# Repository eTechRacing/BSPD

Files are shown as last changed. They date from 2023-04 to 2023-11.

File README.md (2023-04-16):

# BSPD

This repository contains the hardware design files for the Brake System Plausibility Device (BSPD) used in e-Tech Racing's electric vehicle.

## Purpose
The BSPD is a non-programmable circuit that ensures the safe operation of the vehicle during hard braking events. The BSPD must open the shutdown circuit when hard braking occurs, if more than 5kW of power is being delivered to the motors for more than 500ms.

### ⚠️Warning⚠️
Please check for changes in ruling. This BSPD is designed following [FSG Rules from 2023](https://www.formulastudent.de/fileadmin/user_upload/all/2023/rules/FS-Rules_2023_v1.1.pdf).
This version of the BSPD is normally closed when not powered. This could be a potential rules issue, so consider redesigning the relay part for this to be solved.

## Additional hardware
For the BSPD to work, two sensors and a 20-30VDC supply are needed. Here are the ones used in ETR-08:
- [Brake pressure sensor](https://www.amazon.es/gp/product/B07HLKD5L1/ref=ppx_yo_dt_b_asin_title_o01_s00?ie=UTF8&psc=1) : 0.5-4.5V, 1/8", supplied with 5VDC. Bought via Amazon, 25€
- [Hall current sensor](https://www.lem.com/en/product-list/has-100s): In order to measure power, a current sensor is used, so worst case scenario is 5kW / Vmax = 8.5A.

## Installation
- To use the BSPD, follow the installation steps below:

- Connect the brake system pressure sensor to the BSPD.

- Connect the TS current sensor to the BSPD.

- Connect the BSPD to the LVMS.

- Test the BSPD to ensure proper functionality.

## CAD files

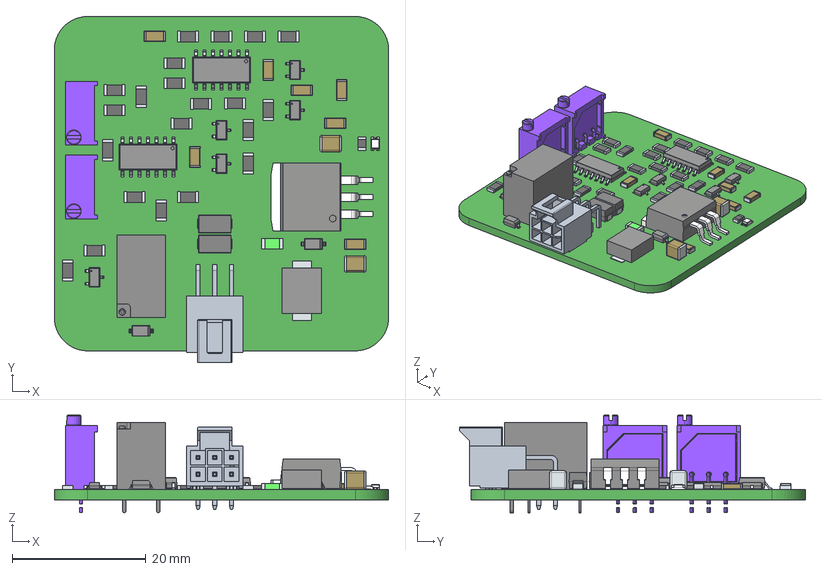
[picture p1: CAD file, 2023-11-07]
BSPD/BSPD_PCB/Project Outputs for BSPD/ExportSTEP/BSPD.step
50.0 x 51.7 x 14.6 mm
3296W-1-100LF x 8
term1 x 23
term2 x 23
150080RS75000
G5V-1-DC5_RGB4408131
PinsArrayLR x 2
BODY-TO
HTSINK-TO263
LEAD-TO263 x 3
PinsArrayL x 5
FilletPinR x 7
FilletPinL x 2
FilletPin1 x 2
FilletPin2 x 2
Pins

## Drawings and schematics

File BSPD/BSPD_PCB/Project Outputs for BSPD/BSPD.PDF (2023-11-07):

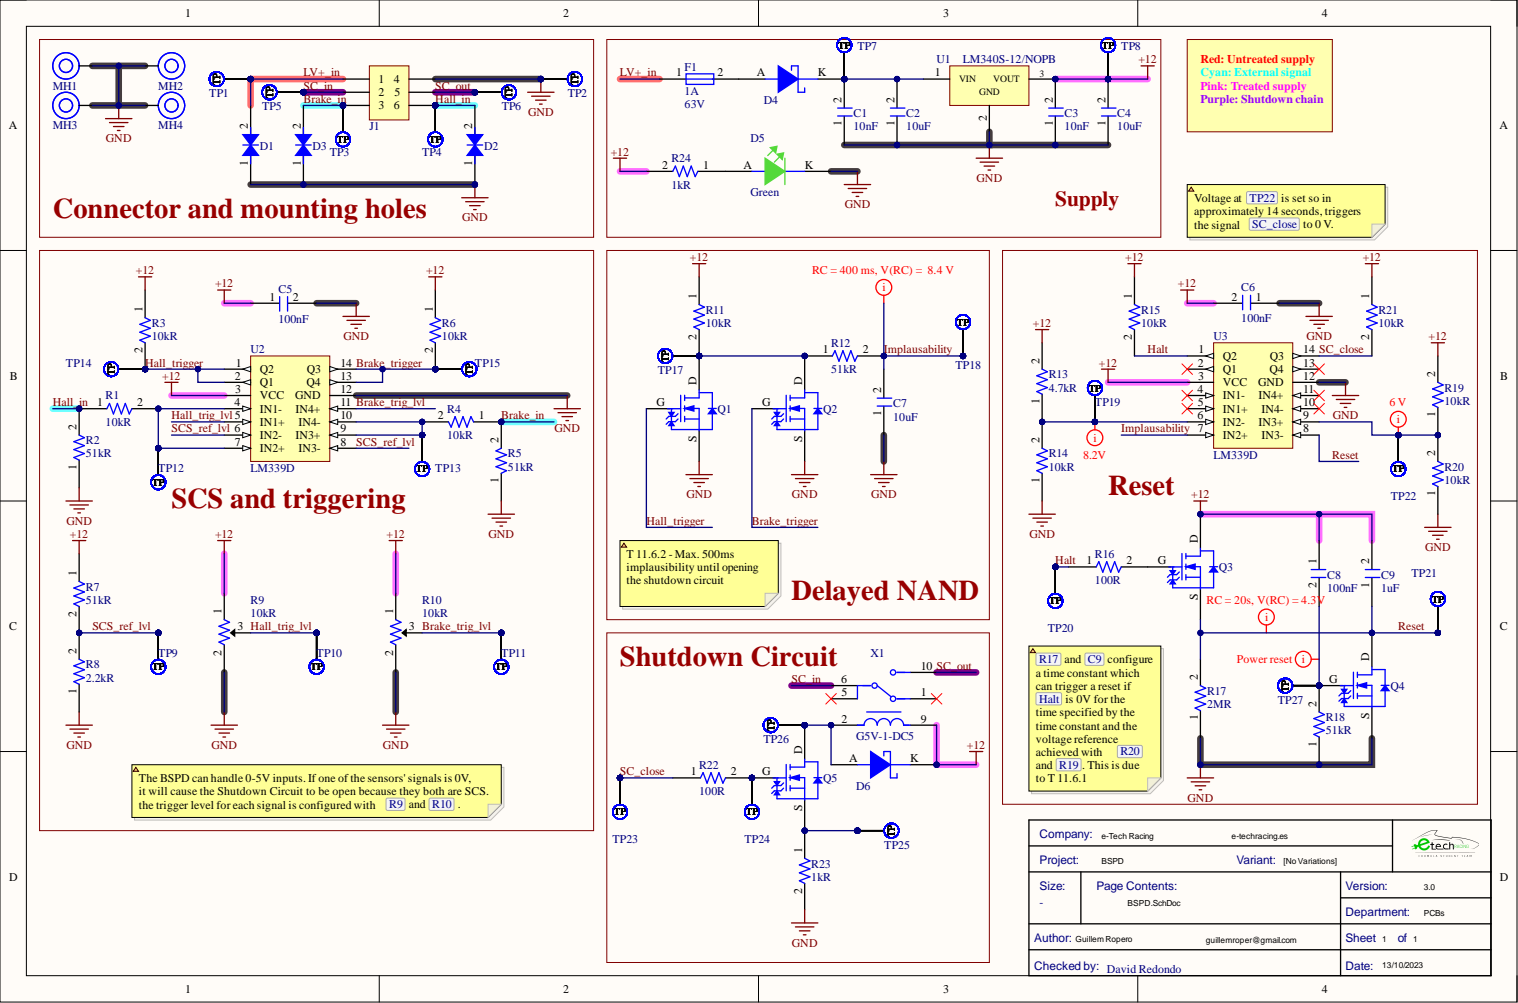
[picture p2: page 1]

Voltage at TP22 is set so in
approximately 14 seconds, triggers
the signal SC_close to 0 V.

Connector and mounting holes

R17 and C9 configure
a time constant which
can trigger a reset if
Halt is 0V for the
time specified by the
time constant and the
voltage reference
and R19 . This is due

The BSPD can handle 0-5V inputs. If one of the sensors' signals is 0V,
it will cause the Shutdown Circuit to be open because they both are SCS.

Author: Guillem Ropero guillemroper@gmail.com | Sheet 1 of 1

Checked by: David Redondo | Date: 13/10/2023

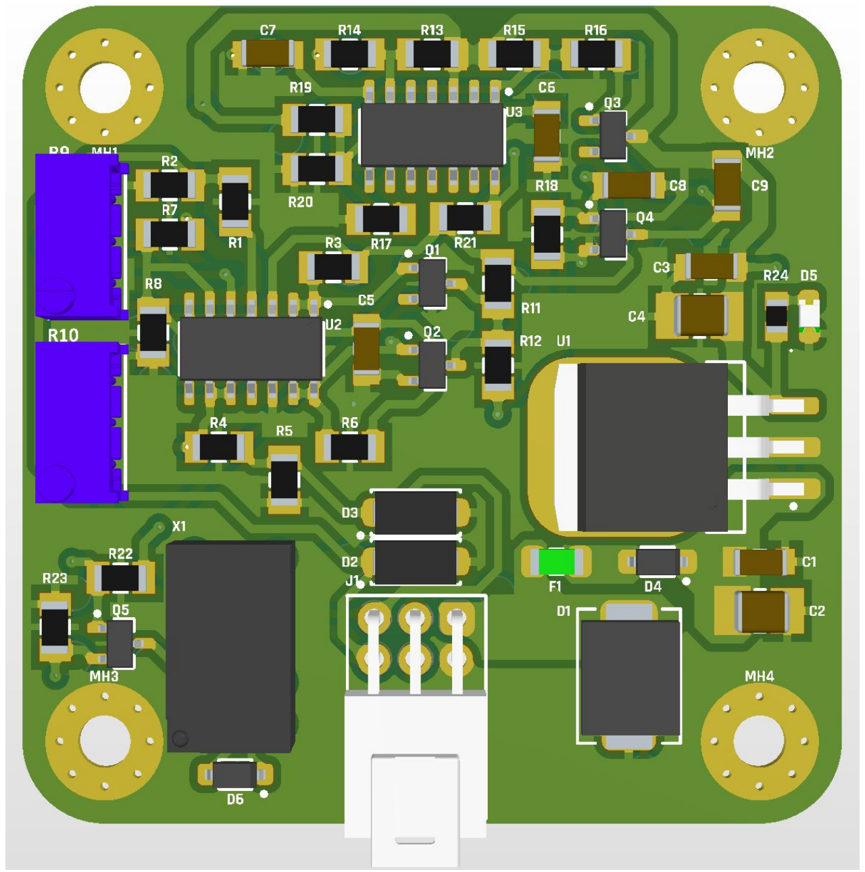
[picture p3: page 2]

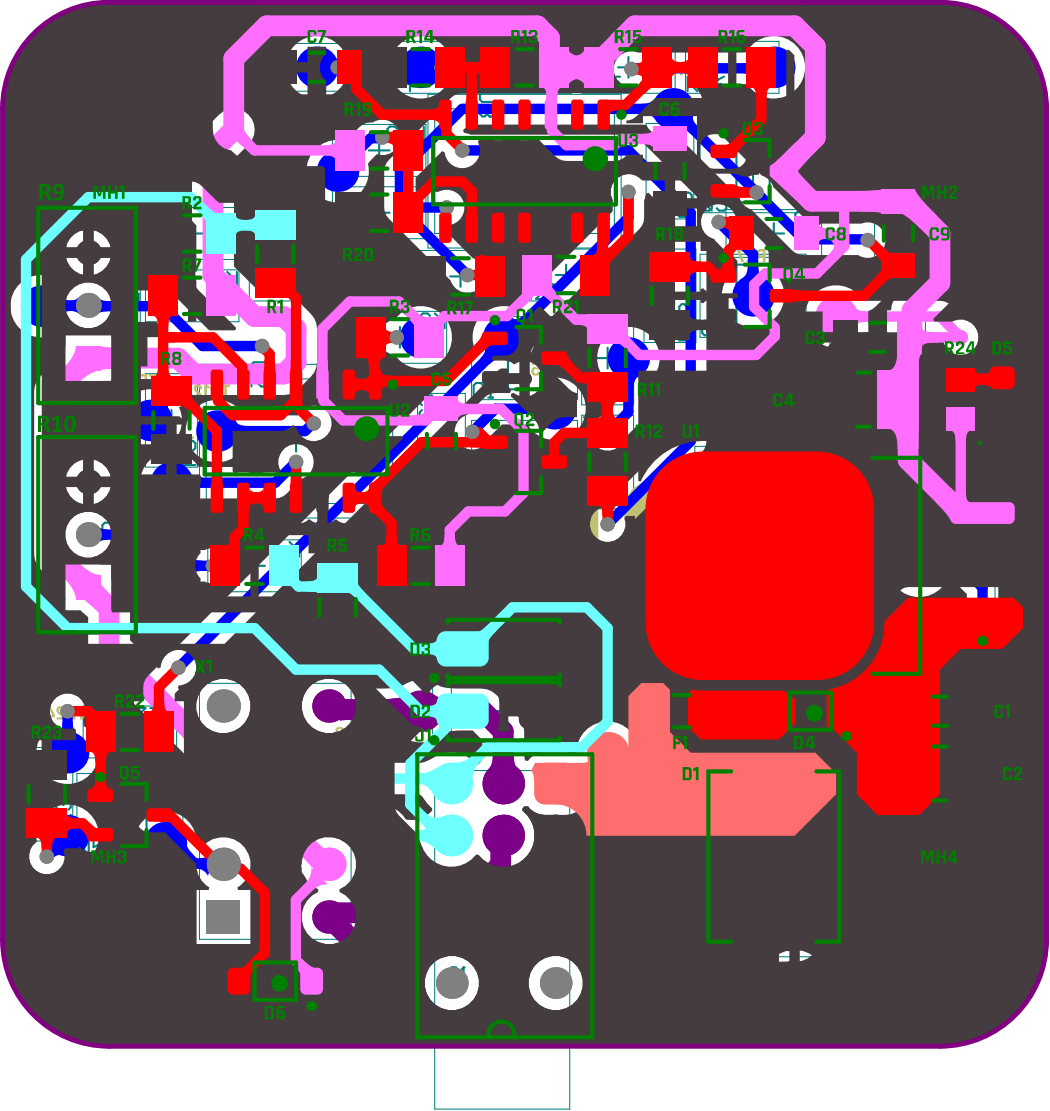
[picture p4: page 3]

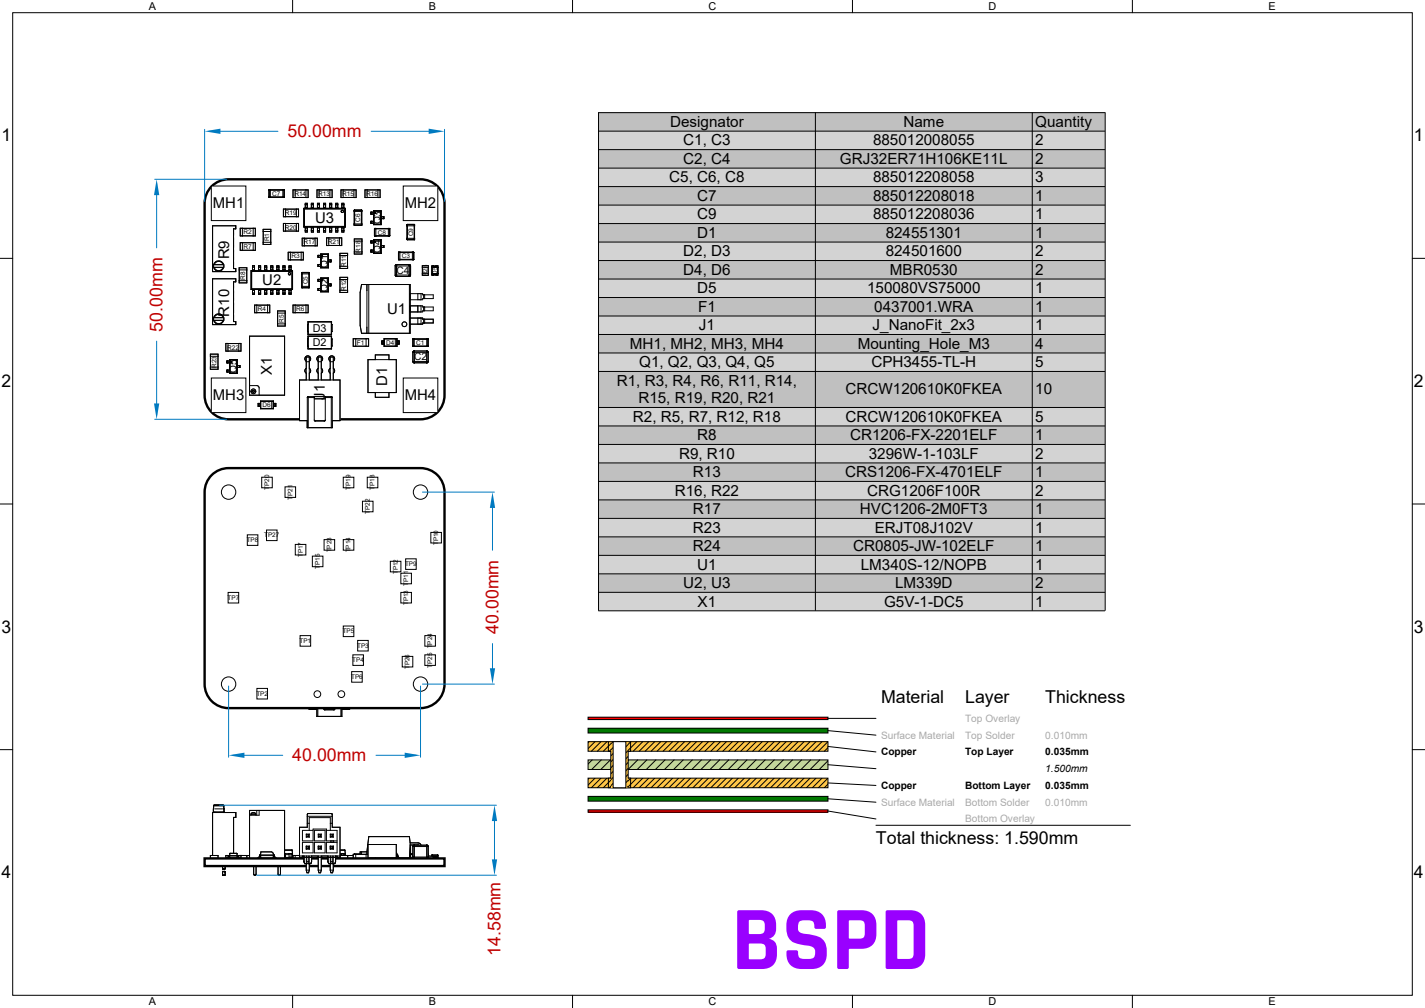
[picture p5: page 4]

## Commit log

2022-03-11 reestructuracion carpetas
    [BSPD.PrjPCB, BSPD_Input.SchDoc, BSPD_Latching.SchDoc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]
2022-12-11 final version, ready for production
    [BSPD.GBL, BSPD.GBO, BSPD.GBP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]
2023-03-28 Modificación en el esquemático del delayed NAND para cumplir con la normativa del ESF, R12 con valor de 30kR para que RC=400ms
    [BSPD.PcbDoc, BSPD.PrjPCB, BSPD.SchDoc]
2023-04-01 BSPD actualizada con los potenciometros correctos y el relé bien configurado (supuestamente)
    [BSPD.PcbDoc, BSPD.PrjPCB, BSPD.SchDoc]
2023-10-13 Update of BSPD
    Solved the issue regarding the proper functioning of the Pcb. Logic gate made by nMOSFETs Q1 and Q2 has been modified, so when power and braking occurs, Shutdown chain opens.
    [BSPD.GBL, BSPD.GBO, BSPD.GBP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]
2023-10-13 Update from last commit
    Correction of shutdown circuit (Relay X1 pads): now when BSPD is not powered, Shutdown chain remains open.
    [BSPD.PcbDoc, BSPD.SchDoc]
